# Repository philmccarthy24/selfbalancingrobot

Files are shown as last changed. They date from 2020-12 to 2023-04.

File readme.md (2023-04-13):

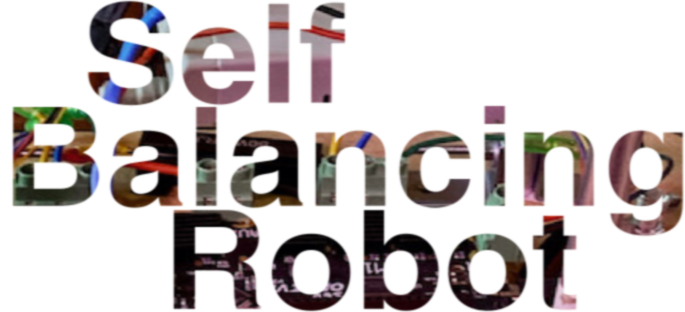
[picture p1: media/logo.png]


## Introduction

A project to explore how self balancing vehicles like the Segway / hoverboards work. This will be a long running spare-time project.

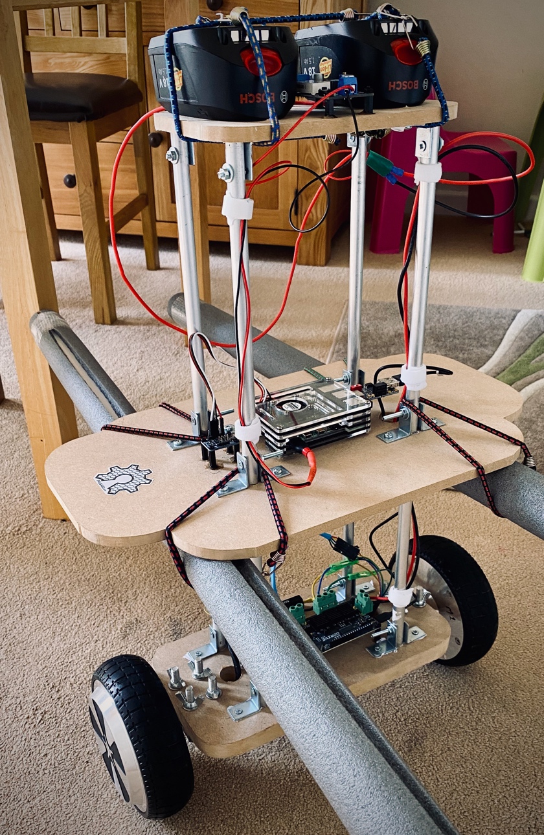
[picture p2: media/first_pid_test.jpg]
first test


## Hardware spec

The robot has been built using:

- 3 layers of MDF, the bottom 18mm thick and the top two 9mm thick
- 4 12mm diameter hollow aluminium poles 50mm in length slotted and bolted through the middle sheet to give strength and stability while keeping the assembly relatively lightweight - fully built, the robot has XX g mass.
- 28 25mm steel braces and 16 M4 bolts/washers/nuts to secure the poles to the boards.
- 2 6.5 inch 36v rated wheel hub motors taken from a broken hoverhoard bought off ebay for £20, each secured with 4 M8 bolts, washers and wing nuts.

See the mechanical drawings in the docs/mechanical directory for further details (created with [OpenSCAD](https://openscad.org/)). Here's a photo of the assembly during motor/ahrs testing, showing how the frame is bolted together:

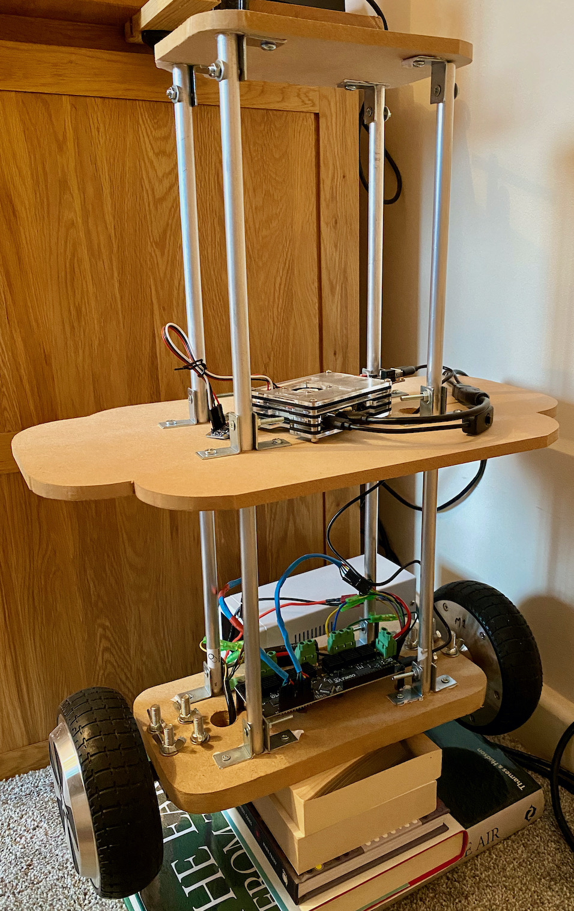
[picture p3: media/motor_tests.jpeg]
motor tests


## Electronics

The motor driver runs on 36v from two 18v LIon batteries I had knocking about from a dead electric screwdriver. 

The controller runs off a separate 18650 LIon battery (to prevent ground loops via ODrive UART connection) via a 3.7v to 5v up-converter.

A Teensy 4.1 MCU runs the control firmware, and is connected to:

- a FXAS2100 Gyroscope IC over I2C bus
- a FXOS8700 Accelerometer/Magnetometer IC over I2C bus
- a 128x64 OLED display over I2C bus
- 3 rotary encoders for user interaction
- a 18-56v [ODrive 3.6 BLDC motor controller board](https://odriverobotics.com) over a serial link at 115200 baud

The sensor hardware containing the gyro/accelerometer/mag sensors is an [Adafruit NXP 9-DOF Breakout Board](https://www.adafruit.com/product/3463).

The wheel hub motors are driven by the ODrive at 36v.

## Firmware

Coded using Arduino IDE, the firmware separates concerns using a basic (synchronous) EventBus PUB/SUB design, to decouple the different elements and allow classes to house library setup boilerplate. 

In this way, the main .ino sketch is kept minimal. `UserInterface` contains a state machine that describes which mode the controller is in. `RotaryEncoder` objects raise position update or button pushed events which are received by the `UserInterface` object, and depending on state either change between screens or allow PID contants to be tweaked (possibly more settings can be managed in future). The main loop periodically fires a timer message at 100Hz, which is received by the `AHRS` object. The handler then reads gyro/accelerometer/magnetometer raw counts from the NXP sensor module, applies NXP/Kalman sensor fusion, and then publishes an AHRS update message on the bus.
`UserInterface` reads AHRS messages and displays data to the screen every 200ms (to avoid timings going out of sync).

`MotionController` also receives AHRS update messages, and uses the values in a PID controller to command the ODrive via serial link to apply current to the wheel motors to keep the robot upright (by moving the robot to keep the weight over the wheels).

## Project restart April 2023

Initially the project used a Raspberry Pi 4 to control the ODrive. I could not get the robot to balance, experiencing violent wheel oscillation motion and instability despite experimenting with lots of PID values. Eventually the ODrive stopped driving one of the motors after a firmware update and failed recalibration.

Several things were wrong with this approach:

- Using a full Linux computer to perform real time motion control; a dedicated MCU is a better choice and allows timings to be more accurate, free of thread scheduling and OS jitter
- Applying velocity commands to ODrive. Current control is better, proportional to torque and more likely to result in successful balance control
- Not having an immediate way to dynamically tweak PID values, resulting in long experimentation cycles. Rotary Encoders and a little OLED screen will save tons of time.

In early April 2023 I dusted off (literally) the robot, flashed the ODrive with the latest firmware, and tried recalibrating the hub motors from scratch. This time I was successful, probably due to updated firmware and instructions. I managed to create a simple sketch for a Teensy 4.1 to drive the wheels via the ODrive serial pins.

I'm now creating a minimal firmware to periodically take AHRS readings, and apply current to the ODrive via a PID controller.

---

## Progress as of May 2021

- Mechanical frame built.
- 36v (2 x 18v) batteries lashed to top panel with bungee cords, and connected via spade terminals to power bus.
- On/off power rocker switch installed.
- 36v to 5v DC down converter connected to power bus and wired to USB-C cable for Pi4 power.
- Odrive board and wheels installed, wiring complete.
- Pi4 with AHRS breakout installed, wiring complete.
- Basic motor calibration done, tested moving hub motors using serial commands issued from Pi4 daemon. *Optimisation with odrivetool required*
- Attached impact lances to frame, to cushion robot during the rather violent oscillations of PID tuning
- Daemon software 95% implemented
  - CMake build system
  - Factories
  - Logging via spdlog library
  - Unit tests via google test library
  - Performance unit tests written to test AHRS at rest and drive motors via ODrive
  - AHRS system to determine orientation in 3D space
  - Gyroscope, accelerometer and magnetometer sensor calibration tool finished, and used to calibrate sensors in-situ after installation on chassis
  - Motor controller api
  - PID controller
- UI software barely started
  - Non-TS React interface started
  - Tested against a fake REST controller served by Node.js
  
#### TO DO:

- Write gRPC service in daemon to support remote drive control
- Complete React UI
- Complete tuning PID controller to make the robot stay up. 

## License/legal

Copyright (c) 2021 Phil McCarthy

Provided under the [MIT License](https://github.com/philmccarthy24/selfbalancingrobot/blob/8f1a7e7f0787cc03bbfced4b563601a9d68a3980/LICENSE).

The software uses the following open source libraries, with thanks and appreciation to their maintainers:

- [Bosch Power4All adapter design](https://github.com/usedbytes/power4all) base part Copyright 2020 Brian Starkey
- Adafruit SSD1306 and dependencies (OLED)
- Encoder (rotary encoders)
- Afafruit_AHRS (with FXOS/FXAS deps)
- [ODrive Arduino](https://github.com/odriverobotics/ODrive/tree/master/Arduino/ODriveArduino)

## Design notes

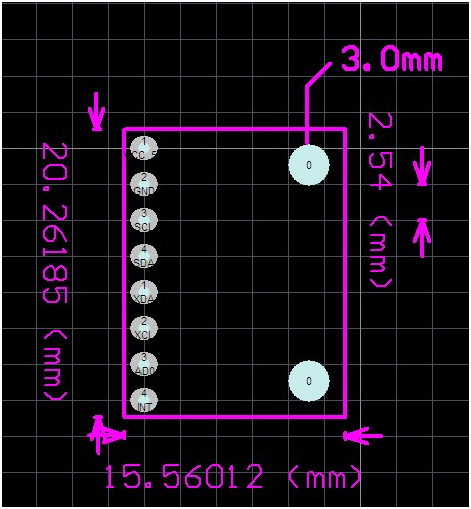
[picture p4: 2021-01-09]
docs/mechanical/MPU6050-Dimensions.png

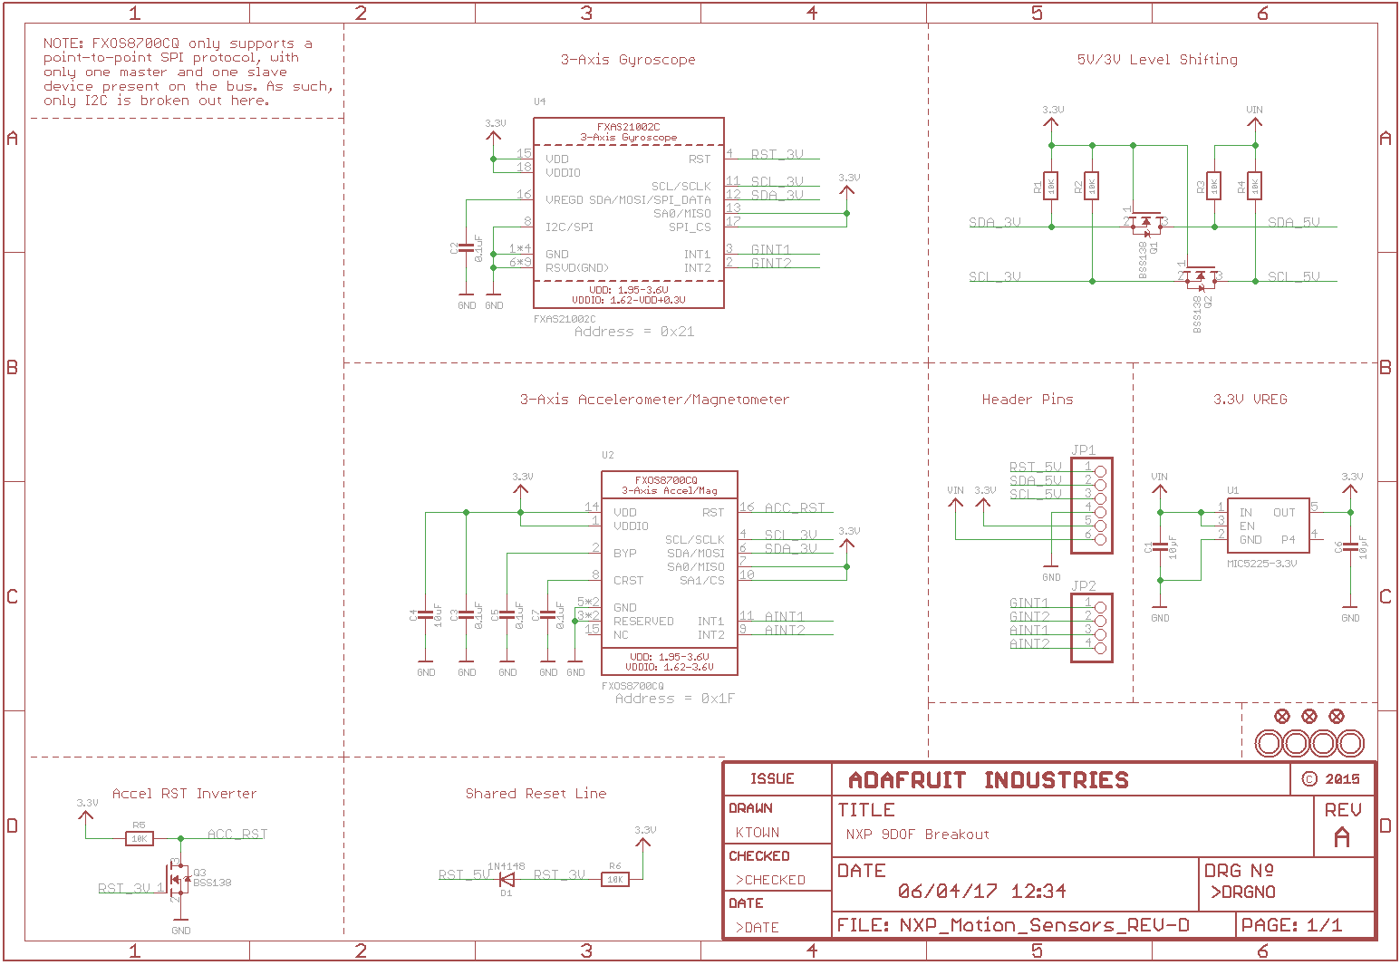
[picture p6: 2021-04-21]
docs/sensors_NXPPrecision9DOF.png

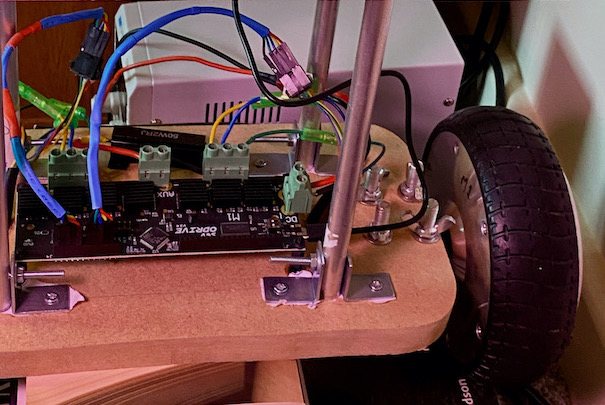
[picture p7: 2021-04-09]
media/controller.jpeg

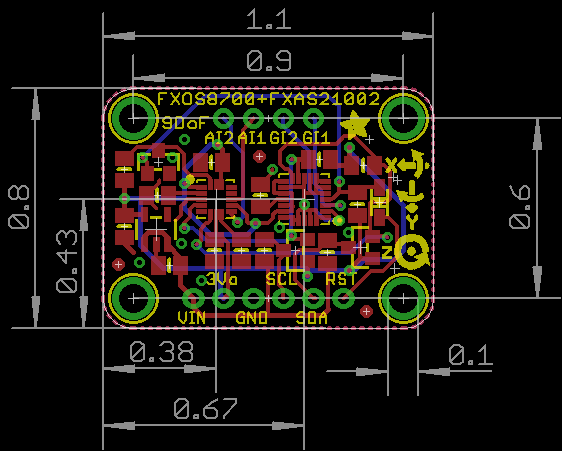
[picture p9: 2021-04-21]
docs/nxp_precision_9dof_breakout.png

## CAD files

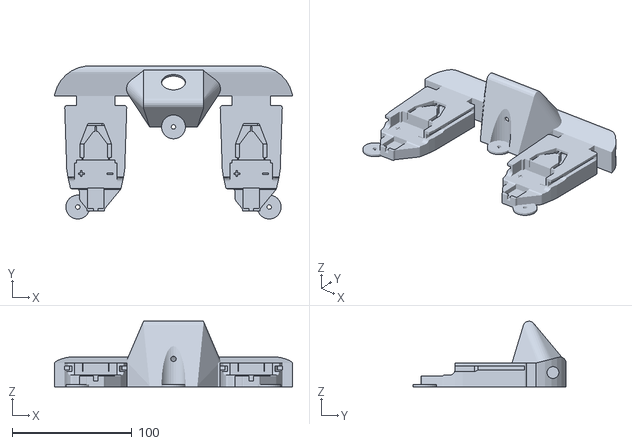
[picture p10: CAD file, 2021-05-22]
cad/batterymount/power4allmount.stl
198.9 x 127.8 x 55.0

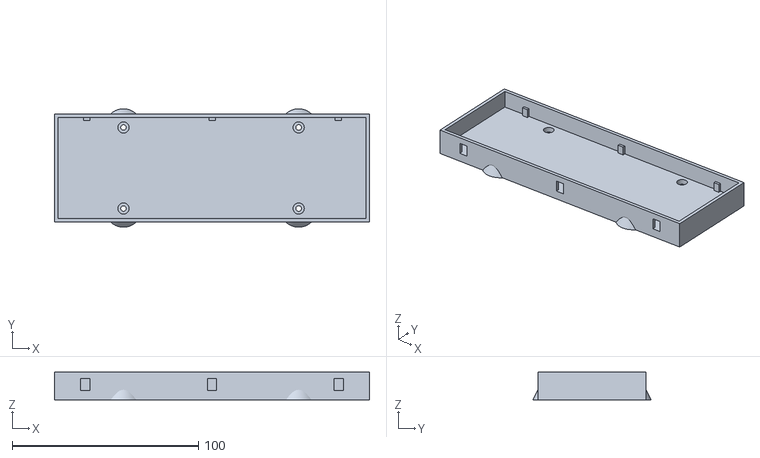
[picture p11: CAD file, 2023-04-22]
cad/stl/prototype_breadboard_mount.stl
169.0 x 63.5 x 15.0

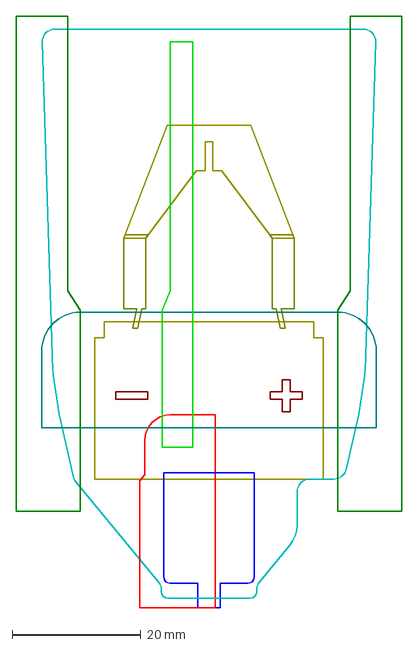
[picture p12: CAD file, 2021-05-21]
cad/batterymount/power4all.dxf
60.0 x 92.0 mm

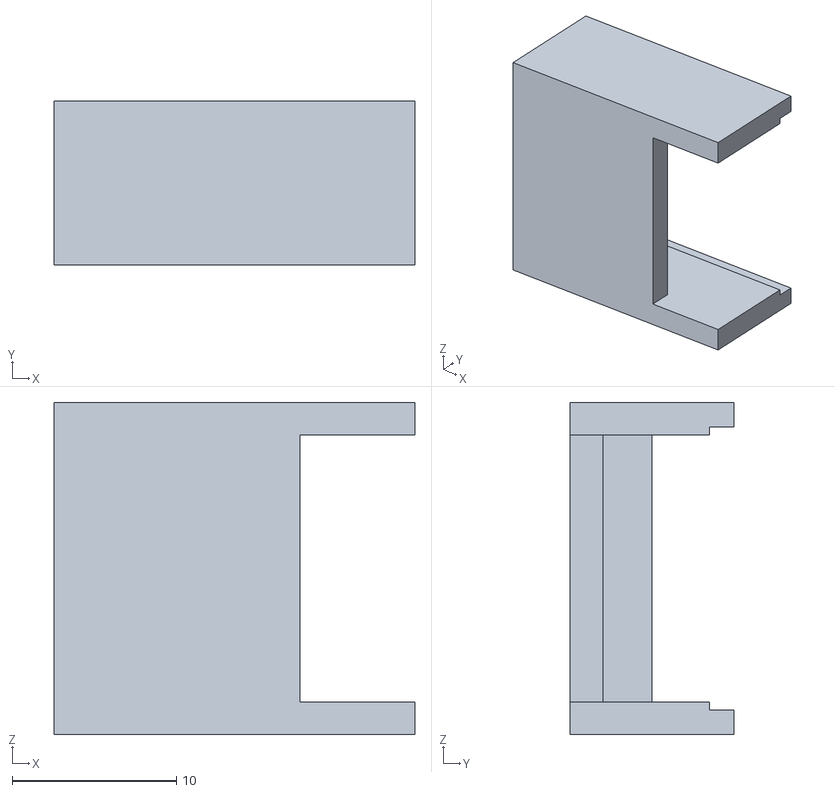
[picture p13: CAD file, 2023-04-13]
cad/stl/tp4056mount.stl
22.0 x 10.0 x 20.2

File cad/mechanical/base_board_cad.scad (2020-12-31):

// globals
board_width = 295;
board_height = 150;

include <common.scad>

difference() {
    union() {
        rounded_rectangle(board_width, board_height, 30);
    }
    
    union() {
        stator_axle_plate_width = 40;
        stator_axle_plate_height = 44;
        axle_plate_bolt_holes = [[7.5, 6.5], [32, 6.5], [7.5, 36.5], [32, 36.5]];
        // left plate bolt holes
        // to secure stator axle, will need M8 bolts at least 55mm shaft length (not including head. head diameter must be no more than 12mm)
        circle_group( axle_plate_bolt_holes, 8, [0, (board_height/2) - (stator_axle_plate_height/2)]);
        
        // left cable hole
        offset_circle([stator_axle_plate_width + 20, board_height/2], 20);
       
        // odrive mounting holes
        odrive_width = 140.5;
        odrive_height = 50;
        odrive_left_edge = stator_axle_plate_width + 20 + 20;
        odrive_standoff_mounting_holes = [[2.5,4], [2.5,47.5], [55,5.5], [55,29.1], [93.5,5.5], [93.5,29.1], [138,4], [138,47.5]];
        circle_group( odrive_standoff_mounting_holes, 6, [odrive_left_edge, (board_height/2) - (odrive_height/2) + 15]);
        
        // support rods and mounting bracket holes
        top_board_pt_offset = [(board_width/2) - (top_board_width/2),board_height-top_board_height-5];
        support_rods_and_bracket_holes(true, top_board_pt_offset);
        
        // right cable hole
        offset_circle([odrive_left_edge + odrive_width + 15, board_height/2], 20);
        
        // right plate bolt holes
        circle_group( axle_plate_bolt_holes, 8, [board_width-stator_axle_plate_width, (board_height/2) - (stator_axle_plate_height/2)]);
    }
}

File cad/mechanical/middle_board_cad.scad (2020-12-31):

// globals
board_width_extent = 295+140;
board_height_extent = 250;

include <common.scad>

top_board_pt_offset = [(board_width_extent/2) - (top_board_width/2),(board_height_extent/2)-(top_board_height/2)];

difference() {
    union() {
        translate([0,20])
            rounded_rectangle(board_width_extent, board_height_extent*0.7, 50);
        
        middle_section_width = board_width_extent*0.75;
        translate([(board_width_extent/2)-(middle_section_width/2),0])
            rounded_rectangle(middle_section_width, board_height_extent, 50);
    }
    
    union() {
        support_rods_and_bracket_holes(true, top_board_pt_offset);
        
        // cable and data hole
        translate([20,top_board_height-50])
            offset_circle(top_board_pt_offset, 20);
    }
}

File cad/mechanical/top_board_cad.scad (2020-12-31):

include <common.scad>

difference() {
    union() {
        rounded_rectangle(top_board_width, top_board_height, 30);
    }
    
    union() {
        support_rods_and_bracket_holes(false);
    }
}

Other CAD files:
cad/batterymount/power4all.scad
cad/batterymount/power4allmount.scad
cad/mcuenclosure/powermodule.scad
cad/mcuenclosure/prototype_powerbank_mount.scad
cad/mechanical/common.scad

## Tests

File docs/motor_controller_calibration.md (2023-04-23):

# Reproduction steps for motor controller calibration

## Hardware

- ODrive 3.6 56v version https://odriverobotics.com
- 2 x 6.5" 36V Hoverboard wheels (Lanba36V20B191025724/800 - SN?)
- 36V power supply
- Raspberry PI 4 running off seperate power supply to avoid ground loops

### Wiring setup

Follow [the ODrive setup guide](https://docs.odriverobotics.com/) for the hardware connection guide (diagram below)

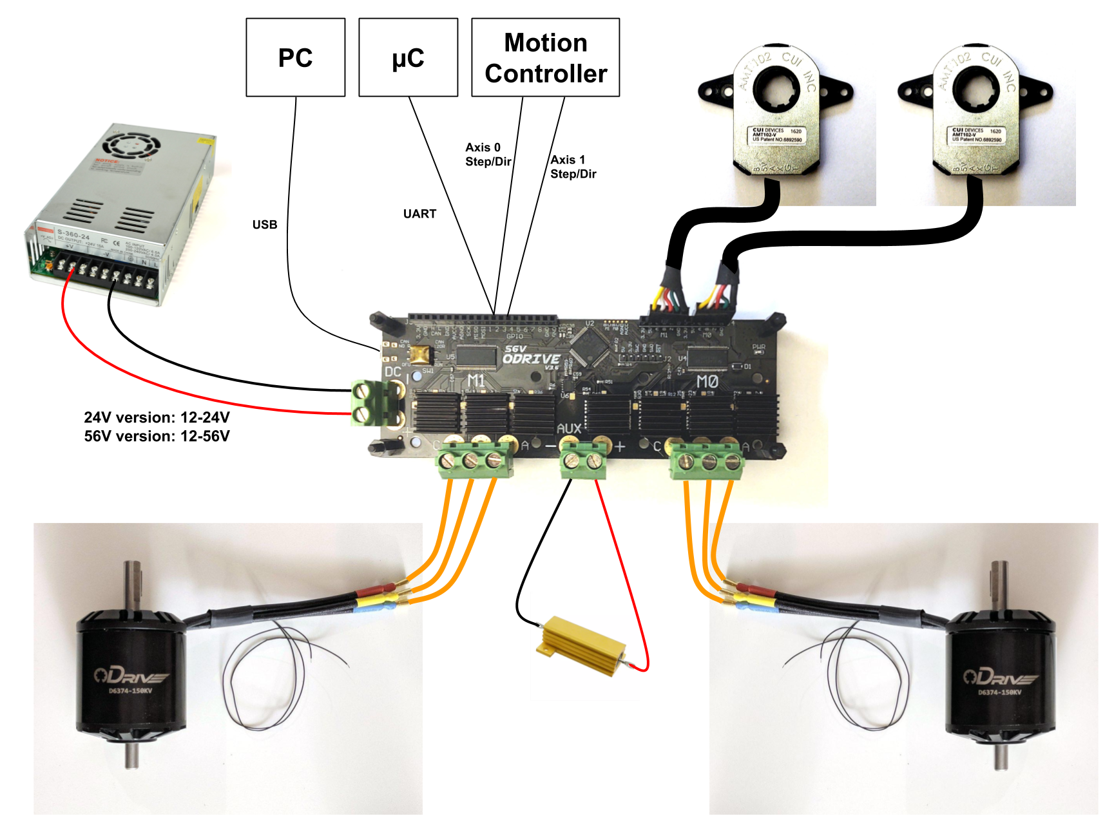
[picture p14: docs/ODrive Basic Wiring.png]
Wiring guide


#### Hall sensor wiring

- Red : 5V
- Yellow : A
- Blue : B
- Green : Z
- Black : GND

# Software

On Raspberry PI

```
sudo pip3 install --upgrade odrive
sudo odrivetool
```

Should now be in interactive ODrive tool ready to issue setup / calibration commands.

Hoverboard specific guide is [here](https://docs.odriverobotics.com/v/0.5.5/hoverboard.html#hoverboard-doc), info extracted and summarised for posterity. This is what worked for me and the second hand hoverboard motors after some tweaking and errors about motor phase inductance.
Set axis0 or axis1 depending on if M0 or M1 is being setup.

```
odrv0.axis0.motor.config.pole_pairs = 15

odrv0.axis0.motor.config.resistance_calib_max_voltage = 4
odrv0.axis0.motor.config.calibration_current = 5 # this was added to get calib to work - NOT IN GUIDE. default was 10
odrv0.axis0.motor.config.requested_current_range = 25 #Requires config save and reboot
odrv0.axis0.motor.config.current_control_bandwidth = 100
odrv0.axis0.motor.config.torque_constant = 8.27 / 16

odrv0.axis0.encoder.config.mode = ENCODER_MODE_HALL
odrv0.axis0.encoder.config.cpr = 90
odrv0.axis0.encoder.config.calib_scan_distance = 150
odrv0.config.gpio9_mode = GPIO_MODE_DIGITAL
odrv0.config.gpio10_mode = GPIO_MODE_DIGITAL
odrv0.config.gpio11_mode = GPIO_MODE_DIGITAL

odrv0.axis0.encoder.config.bandwidth = 100
odrv0.axis0.controller.config.pos_gain = 1
odrv0.axis0.controller.config.vel_gain = 0.02 * odrv0.axis0.motor.config.torque_constant * odrv0.axis0.encoder.config.cpr
odrv0.axis0.controller.config.vel_integrator_gain = 0.1 * odrv0.axis0.motor.config.torque_constant * odrv0.axis0.encoder.config.cpr
odrv0.axis0.controller.config.vel_limit = 10
odrv0.axis0.controller.config.control_mode = CONTROL_MODE_VELOCITY_CONTROL

odrv0.save_configuration()
odrv0.reboot()

# do the calibration
odrv0.axis0.requested_state = AXIS_STATE_MOTOR_CALIBRATION

# read out data pertaining to motor
odrv0.axis0.motor

# error should be 0x0000 and phase_inductance / phase_resistance should be set (not 0.0)
# tell the ODrive that saving this calibration to persistent memory is OK
odrv0.axis0.motor.config.pre_calibrated = True

odrv0.axis0.requested_state = AXIS_STATE_ENCODER_HALL_POLARITY_CALIBRATION

# read out status of encoder
odrv0.axis0.encoder

# error should be 0x0000

# check the alignment between the motor and the hall sensor
odrv0.axis0.requested_state = AXIS_STATE_ENCODER_OFFSET_CALIBRATION

# read out status of encoder
odrv0.axis0.encoder

# error should be 0x0000 and phase_offset_float should be -1.5, -0.5, 0.5 or 1.5
# tell the ODrive that saving this calibration to persistent memory is OK
odrv0.axis0.encoder.config.pre_calibrated = True

# Save, reboot, and test! ODrive starts in IDLE by default (can configure this), so need to enable closed loop control.
odrv0.save_configuration()
odrv0.reboot()

odrv0.axis0.requested_state = AXIS_STATE_CLOSED_LOOP_CONTROL
odrv0.axis0.controller.input_vel = 2
# Your motor should spin here!!!!
odrv0.axis0.controller.input_vel = 0
odrv0.axis0.requested_state = AXIS_STATE_IDLE
```

Repeat for axis1 (text here for easy copy-paste):

```
odrv0.axis1.motor.config.pole_pairs = 15

odrv0.axis1.motor.config.resistance_calib_max_voltage = 4
odrv0.axis1.motor.config.calibration_current = 5 # this was added to get calib to work - NOT IN GUIDE. default was 10
odrv0.axis1.motor.config.requested_current_range = 25 #Requires config save and reboot
odrv0.axis1.motor.config.current_control_bandwidth = 100
odrv0.axis1.motor.config.torque_constant = 8.27 / 16

odrv0.axis1.encoder.config.mode = ENCODER_MODE_HALL
odrv0.axis1.encoder.config.cpr = 90
odrv0.axis1.encoder.config.calib_scan_distance = 150
odrv0.config.gpio9_mode = GPIO_MODE_DIGITAL
odrv0.config.gpio10_mode = GPIO_MODE_DIGITAL
odrv0.config.gpio11_mode = GPIO_MODE_DIGITAL

odrv0.axis1.encoder.config.bandwidth = 100
odrv0.axis1.controller.config.pos_gain = 1
odrv0.axis1.controller.config.vel_gain = 0.02 * odrv0.axis0.motor.config.torque_constant * odrv0.axis0.encoder.config.cpr
odrv0.axis1.controller.config.vel_integrator_gain = 0.1 * odrv0.axis0.motor.config.torque_constant * odrv0.axis0.encoder.config.cpr
odrv0.axis1.controller.config.vel_limit = 10
odrv0.axis1.controller.config.control_mode = CONTROL_MODE_VELOCITY_CONTROL

odrv0.save_configuration()
odrv0.reboot()

# do the calibration
odrv0.axis1.requested_state = AXIS_STATE_MOTOR_CALIBRATION

# read out data pertaining to motor
odrv0.axis1.motor

# error should be 0x0000 and phase_inductance / phase_resistance should be set (not 0.0)
# tell the ODrive that saving this calibration to persistent memory is OK
odrv0.axis1.motor.config.pre_calibrated = True

odrv0.axis1.requested_state = AXIS_STATE_ENCODER_HALL_POLARITY_CALIBRATION

# read out status of encoder
odrv0.axis1.encoder

# error should be 0x0000

# check the alignment between the motor and the hall sensor
odrv0.axis1.requested_state = AXIS_STATE_ENCODER_OFFSET_CALIBRATION

# read out status of encoder
odrv0.axis1.encoder

# error should be 0x0000 and phase_offset_float should be -1.5, -0.5, 0.5 or 1.5
# tell the ODrive that saving this calibration to persistent memory is OK
odrv0.axis1.encoder.config.pre_calibrated = True

# Save, reboot, and test! ODrive starts in IDLE by default (can configure this), so need to enable closed loop control.
odrv0.save_configuration()
odrv0.reboot()

odrv0.axis1.requested_state = AXIS_STATE_CLOSED_LOOP_CONTROL
odrv0.axis1.controller.input_vel = 2
# Your motor should spin here!!!!
odrv0.axis1.controller.input_vel = 0
odrv0.axis1.requested_state = AXIS_STATE_IDLE
```

We then need to put the odrive in TORQUE_CONTROL mode with 

```
odrv0.axis0.controller.config.control_mode = ControlMode.TORQUE_CONTROL
odrv0.axis1.controller.config.control_mode = ControlMode.TORQUE_CONTROL
odrv0.axis0.controller.config.enable_torque_mode_vel_limit = False
odrv0.axis1.controller.config.enable_torque_mode_vel_limit = False

```

May also need to disable current limits

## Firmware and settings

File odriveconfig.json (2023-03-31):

{"axis0": {"acim_estimator": {"config": {"slip_velocity": 14.706000328063965}}, "config": {"dir_gpio_pin": 2, "enable_sensorless_mode": false, "enable_step_dir": false, "enable_watchdog": false, "startup_closed_loop_control": false, "startup_encoder_index_search": false, "startup_encoder_offset_calibration": false, "startup_homing": false, "startup_motor_calibration": false, "step_dir_always_on": false, "step_gpio_pin": 1, "watchdog_timeout": 0.0, "calibration_lockin": {"accel": 20.0, "current": 10.0, "ramp_distance": 3.1415927410125732, "ramp_time": 0.4000000059604645, "vel": 40.0}, "can": {"encoder_rate_ms": 10, "heartbeat_rate_ms": 100, "is_extended": false, "node_id": 0}, "general_lockin": {"accel": 20.0, "current": 10.0, "finish_distance": 100.0, "finish_on_distance": false, "finish_on_enc_idx": false, "finish_on_vel": false, "ramp_distance": 3.1415927410125732, "ramp_time": 0.4000000059604645, "vel": 40.0}, "sensorless_ramp": {"accel": 200.0, "current": 10.0, "finish_distance": 100.0, "finish_on_distance": false, "finish_on_enc_idx": false, "finish_on_vel": true, "ramp_distance": 3.1415927410125732, "ramp_time": 0.4000000059604645, "vel": 400.0}}, "controller": {"config": {"axis_to_mirror": 255, "circular_setpoint_range": 1.0, "circular_setpoints": false, "control_mode": 2, "electrical_power_bandwidth": 20.0, "enable_gain_scheduling": false, "enable_overspeed_error": true, "enable_torque_mode_vel_limit": true, "enable_vel_limit": true, "gain_scheduling_width": 10.0, "homing_speed": 0.25, "inertia": 0.0, "input_filter_bandwidth": 2.0, "input_mode": 1, "load_encoder_axis": 0, "mechanical_power_bandwidth": 20.0, "mirror_ratio": 1.0, "pos_gain": 1.0, "spinout_electrical_power_threshold": 10.0, "spinout_mechanical_power_threshold": -10.0, "steps_per_circular_range": 1024, "torque_mirror_ratio": 0.0, "torque_ramp_rate": 0.009999999776482582, "vel_gain": 0.9303750395774841, "vel_integrator_gain": 4.6518754959106445, "vel_integrator_limit": Infinity, "vel_limit": 10.0, "vel_limit_tolerance": 1.2000000476837158, "vel_ramp_rate": 1.0, "anticogging": {"anticogging_enabled": true, "calib_anticogging": false, "calib_pos_threshold": 1.0, "calib_vel_threshold": 1.0, "cogging_ratio": 1.0, "index": 0, "pre_calibrated": false}}}, "encoder": {"config": {"abs_spi_cs_gpio_pin": 1, "bandwidth": 100.0, "calib_range": 0.019999999552965164, "calib_scan_distance": 150.0, "calib_scan_omega": 12.566370964050293, "cpr": 90, "direction": 1, "enable_phase_interpolation": true, "find_idx_on_lockin_only": false, "hall_polarity_calibrated": true, "hall_polarity": 0, "ignore_illegal_hall_state": false, "index_offset": 0.0, "mode": 1, "phase_offset_float": 1.4461486339569092, "phase_offset": 69, "pre_calibrated": true, "sincos_gpio_pin_cos": 4, "sincos_gpio_pin_sin": 3, "use_index_offset": true, "use_index": false}}, "max_endstop": {"config": {"debounce_ms": 50, "enabled": false, "gpio_num": 0, "is_active_high": false, "offset": 0.0}}, "mechanical_brake": {"config": {"gpio_num": 0, "is_active_low": true}}, "min_endstop": {"config": {"debounce_ms": 50, "enabled": false, "gpio_num": 0, "is_active_high": false, "offset": 0.0}}, "motor": {"config": {"I_bus_hard_max": Infinity, "I_bus_hard_min": -Infinity, "I_leak_max": 0.10000000149011612, "R_wL_FF_enable": false, "acim_autoflux_attack_gain": 10.0, "acim_autoflux_decay_gain": 1.0, "acim_autoflux_enable": false, "acim_autoflux_min_Id": 10.0, "acim_gain_min_flux": 10.0, "bEMF_FF_enable": false, "calibration_current": 5.0, "current_control_bandwidth": 100.0, "current_lim_margin": 8.0, "current_lim": 10.0, "dc_calib_tau": 0.20000000298023224, "inverter_temp_limit_lower": 100.0, "inverter_temp_limit_upper": 120.0, "motor_type": 0, "phase_inductance": 0.0006406255415640771, "phase_resistance": 0.553097128868103, "pole_pairs": 15, "pre_calibrated": true, "requested_current_range": 25.0, "resistance_calib_max_voltage": 4.0, "torque_constant": 0.5168750286102295, "torque_lim": Infinity}, "fet_thermistor": {"config": {"enabled": true, "temp_limit_lower": 100.0, "temp_limit_upper": 120.0}}, "motor_thermistor": {"config": {"enabled": false, "gpio_pin": 4, "poly_coefficient_0": 0.0, "poly_coefficient_1": 0.0, "poly_coefficient_2": 0.0, "poly_coefficient_3": 0.0, "temp_limit_lower": 100.0, "temp_limit_upper": 120.0}}}, "sensorless_estimator": {"config": {"observer_gain": 1000.0, "pll_bandwidth": 1000.0, "pm_flux_linkage": 0.0015800000401213765}}, "trap_traj": {"config": {"accel_limit": 0.5, "decel_limit": 0.5, "vel_limit": 2.0}}}, "axis1": {"acim_estimator": {"config": {"slip_velocity": 14.706000328063965}}, "config": {"dir_gpio_pin": 8, "enable_sensorless_mode": false, "enable_step_dir": false, "enable_watchdog": false, "startup_closed_loop_control": false, "startup_encoder_index_search": false, "startup_encoder_offset_calibration": false, "startup_homing": false, "startup_motor_calibration": false, "step_dir_always_on": false, "step_gpio_pin": 7, "watchdog_timeout": 0.0, "calibration_lockin": {"accel": 20.0, "current": 10.0, "ramp_distance": 3.1415927410125732, "ramp_time": 0.4000000059604645, "vel": 40.0}, "can": {"encoder_rate_ms": 10, "heartbeat_rate_ms": 100, "is_extended": false, "node_id": 1}, "general_lockin": {"accel": 20.0, "current": 10.0, "finish_distance": 100.0, "finish_on_distance": false, "finish_on_enc_idx": false, "finish_on_vel": false, "ramp_distance": 3.1415927410125732, "ramp_time": 0.4000000059604645, "vel": 40.0}, "sensorless_ramp": {"accel": 200.0, "current": 10.0, "finish_distance": 100.0, "finish_on_distance": false, "finish_on_enc_idx": false, "finish_on_vel": true, "ramp_distance": 3.1415927410125732, "ramp_time": 0.4000000059604645, "vel": 400.0}}, "controller": {"config": {"axis_to_mirror": 255, "circular_setpoint_range": 1.0, "circular_setpoints": false, "control_mode": 2, "electrical_power_bandwidth": 20.0, "enable_gain_scheduling": false, "enable_overspeed_error": true, "enable_torque_mode_vel_limit": true, "enable_vel_limit": true, "gain_scheduling_width": 10.0, "homing_speed": 0.25, "inertia": 0.0, "input_filter_bandwidth": 2.0, "input_mode": 1, "load_encoder_axis": 1, "mechanical_power_bandwidth": 20.0, "mirror_ratio": 1.0, "pos_gain": 1.0, "spinout_electrical_power_threshold": 10.0, "spinout_mechanical_power_threshold": -10.0, "steps_per_circular_range": 1024, "torque_mirror_ratio": 0.0, "torque_ramp_rate": 0.009999999776482582, "vel_gain": 0.9303750395774841, "vel_integrator_gain": 4.6518754959106445, "vel_integrator_limit": Infinity, "vel_limit": 10.0, "vel_limit_tolerance": 1.2000000476837158, "vel_ramp_rate": 1.0, "anticogging": {"anticogging_enabled": true, "calib_anticogging": false, "calib_pos_threshold": 1.0, "calib_vel_threshold": 1.0, "cogging_ratio": 1.0, "index": 0, "pre_calibrated": false}}}, "encoder": {"config": {"abs_spi_cs_gpio_pin": 1, "bandwidth": 100.0, "calib_range": 0.019999999552965164, "calib_scan_distance": 150.0, "calib_scan_omega": 12.566370964050293, "cpr": 90, "direction": 1, "enable_phase_interpolation": true, "find_idx_on_lockin_only": false, "hall_polarity_calibrated": true, "hall_polarity": 0, "ignore_illegal_hall_state": false, "index_offset": 0.0, "mode": 1, "phase_offset_float": 1.4460649490356445, "phase_offset": 69, "pre_calibrated": true, "sincos_gpio_pin_cos": 4, "sincos_gpio_pin_sin": 3, "use_index_offset": true, "use_index": false}}, "max_endstop": {"config": {"debounce_ms": 50, "enabled": false, "gpio_num": 0, "is_active_high": false, "offset": 0.0}}, "mechanical_brake": {"config": {"gpio_num": 0, "is_active_low": true}}, "min_endstop": {"config": {"debounce_ms": 50, "enabled": false, "gpio_num": 0, "is_active_high": false, "offset": 0.0}}, "motor": {"config": {"I_bus_hard_max": Infinity, "I_bus_hard_min": -Infinity, "I_leak_max": 0.10000000149011612, "R_wL_FF_enable": false, "acim_autoflux_attack_gain": 10.0, "acim_autoflux_decay_gain": 1.0, "acim_autoflux_enable": false, "acim_autoflux_min_Id": 10.0, "acim_gain_min_flux": 10.0, "bEMF_FF_enable": false, "calibration_current": 5.0, "current_control_bandwidth": 100.0, "current_lim_margin": 8.0, "current_lim": 10.0, "dc_calib_tau": 0.20000000298023224, "inverter_temp_limit_lower": 100.0, "inverter_temp_limit_upper": 120.0, "motor_type": 0, "phase_inductance": 0.0006110583199188113, "phase_resistance": 0.5124536752700806, "pole_pairs": 15, "pre_calibrated": true, "requested_current_range": 25.0, "resistance_calib_max_voltage": 4.0, "torque_constant": 0.5168750286102295, "torque_lim": Infinity}, "fet_thermistor": {"config": {"enabled": true, "temp_limit_lower": 100.0, "temp_limit_upper": 120.0}}, "motor_thermistor": {"config": {"enabled": false, "gpio_pin": 4, "poly_coefficient_0": 0.0, "poly_coefficient_1": 0.0, "poly_coefficient_2": 0.0, "poly_coefficient_3": 0.0, "temp_limit_lower": 100.0, "temp_limit_upper": 120.0}}}, "sensorless_estimator": {"config": {"observer_gain": 1000.0, "pll_bandwidth": 1000.0, "pm_flux_linkage": 0.0015800000401213765}}, "trap_traj": {"config": {"accel_limit": 0.5,
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

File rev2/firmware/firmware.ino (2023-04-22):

#include <Wire.h>
#include <elapsedMillis.h>
#include "EventBus.h"
#include "RotaryEncoder.h"
#include "UserInterface.h"
#include "AHRS.h"
#include "MotionController.h"
#include <ArduinoLog.h>

EventBus eventBus;
UserInterface gui(&eventBus);
RotaryEncoder dial1(0, 34, 35, 26, &eventBus);
RotaryEncoder dial2(1, 38, 37, 27, &eventBus);
//RotaryEncoder dial3(2, 40, 39, 28, &eventBus);
AHRS ahrs(&eventBus);
MotionController motionController(&eventBus);

elapsedMillis msTimer;
const int AHRS_PERIOD_MS = 1000 / FILTER_UPDATE_RATE_HZ;

void setup() {
  Serial.begin(115200);
  while (!Serial) {} // wait for serial interace to connect

  Log.begin(LOG_LEVEL_VERBOSE, &Serial);

  Log.traceln(F("Setting I2C clock to 400kHz"));
  Wire.setClock(400000); // set I2C clock to 400KHz - ahrs seems to need this

  Log.traceln(F("Setting up event subscriptions..."));
  // setup message subscriptions
  eventBus.Subscribe(&ahrs);
  eventBus.Subscribe(&gui);
  eventBus.Subscribe(&motionController);

  if (!gui.Initialise() || !ahrs.Initialise() || !motionController.Initialise())
    for(;;) // Printed errors to serial already - so spin forever

  Log.traceln(F("Initialised"));
}

void loop() {
  // poll physical controls - this could result in events being fired
  dial1.Poll();
  dial2.Poll();
  //dial3.Poll();

  // publish a timer message every 10ms, to trigger
  // AHRS and then consequentially motion control
  if (msTimer >= AHRS_PERIOD_MS) {
    msTimer = msTimer - AHRS_PERIOD_MS;
    eventBus.Publish(0, EEventType::TimerTimeout, &AHRS_PERIOD_MS);
  }
}

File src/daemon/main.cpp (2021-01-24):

#include <iostream>
#include <memory>
#include <unistd.h>
#include "Register.h"
#include "SBRProdFactory.h"

using namespace std;
using namespace sbrcontroller;

int main()
{
    try {
        // production startup process
        utility::Register::RegisterFactory(make_shared<utility::SBRProdFactory>("./sbrconfig.json"));
        auto ahrsDataSource = utility::Register::Factory.CreateAHRSDataSource();

        for (int i = 0; i < 100; i++) {
            auto currOrientation = ahrsDataSource->ReadOrientation();
            cout << "X rotation " << currOrientation. << " degrees, Y rotation " << currOrientation.m_dbPitch_deg << "degrees" << endl;
            usleep(100 * 1000);
            // seem to be drifting quite a bit (+/- 1degree) even when still. is this
            // sensor noise?
            // https://wired.chillibasket.com/2015/01/calibrating-mpu6050/ has some stuff about
            // fifo. calibrate? read from mp fifo?
            // raw signal synchronisation issue?? https://electronics.stackexchange.com/questions/333174/mpu6050-accel-gyro-noise-that-behaves-strangely-what-might-be-doing-this
        }
    }
    catch (const std::exception& ex) {
        cout << ex.what() << endl;
    }
}

//https://code.visualstudio.com/docs/languages/cpp

//http://wiringpi.com/reference/i2c-library/

//https://sudonull.com/post/97828-Ruby-and-C-Part-4-Friends-of-the-accelerometer-gyroscope-and-range-finder-with-Raphaeljs


//https://wiki.dfrobot.com/How_to_Use_a_Three-Axis_Accelerometer_for_Tilt_Sensing ??

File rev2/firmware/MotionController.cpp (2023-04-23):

#include "MotionController.h"
#include "AHRS.h"
#include <EEPROM.h>
#include <HardwareSerial.h>
#include <ODriveArduino.h>
#include <Wire.h>
#include <Arduino.h>
#include <ArduinoLog.h>

#define MOTION_CONTROLLER_SETTINGS_EEPROM_ADDRESS 140

// Printing with stream operator helper functions
template<class T> inline Print& operator <<(Print &obj,     T arg) { obj.print(arg);    return obj; }
template<>        inline Print& operator <<(Print &obj, float arg) { obj.print(arg, 4); return obj; }

// Teensy 4.1 - Serial1
// pin 0: RX - connect to ODrive TX (GPIO pin 1 on ODrive)
// pin 1: TX - connect to ODrive RX (GPIO pin 2 on ODrive)
HardwareSerial& odrive_serial = Serial1;
ODriveArduino odrive(odrive_serial);

MotionController::MotionController(EventBus* pEventBus) : 
  m_pEventBus(pEventBus)
{
}

bool MotionController::Initialise()
{
  Log.traceln(F("MotionController::Initialise"));

  //read eeprom at offset 140 to get persisted Kp,Ki,Kd constants
  float Kpid[3];
  EEPROM.get(MOTION_CONTROLLER_SETTINGS_EEPROM_ADDRESS,Kpid);
  if (isnan(Kpid[0]) || isnan(Kpid[1]) || isnan(Kpid[2]))
  {
    Log.traceln(F("PID constants not set, initialising to 0.0..."));
    Kpid[0] = 0.0f;
    Kpid[1] = 0.0f;
    Kpid[2] = 0.0f;
    EEPROM.put(MOTION_CONTROLLER_SETTINGS_EEPROM_ADDRESS,Kpid);
    Log.traceln(F("PID constants initialised."));
  }
  m_Kp = Kpid[0];
  m_Ki = Kpid[1];
  m_Kd = Kpid[2];

  Log.traceln(F("Read PID vals from EEPROM: Kp=%F, Kd=%F"), m_Kp, m_Kd);

  // publish a message with read settings, to synchronise interested listeners
  m_pEventBus->Publish(0, EEventType::SettingsSync, Kpid);

  // ODrive uses 115200 baud
  odrive_serial.begin(115200);

  Log.traceln(F("Setting ODrive current limits to 10A per wheel"));
  //odrive_serial << "w axis0.motor.config.current_lim " << 5.0f << '\n';
  //odrive_serial << "w axis1.motor.config.current_lim " << 5.0f << '\n';

  odrive_serial << "w axis0.controller.config.enable_torque_mode_vel_limit false\n";
  odrive_serial << "w axis1.controller.config.enable_torque_mode_vel_limit false\n";

  int requested_state = AXIS_STATE_CLOSED_LOOP_CONTROL;
  Log.traceln(F("Engaging motors"));
  odrive.run_state(0, requested_state, false);
  odrive.run_state(1, requested_state, false);

  return true;
}

void MotionController::OnEventNotify(int sourceId, EEventType type, const void* eventData)
{
  // AHRS updates tick on a 100hz timer, which we will match to control wheel torque.
  // Note we have the flexibility to change this by creating an additional independent timer, caching AHRS
  // update messages and then doing PID processing and motion control on the independent timer tick.

  if (type == EEventType::AHRSUpdate) {
    SOrientationPayload* pOri = (SOrientationPayload*)eventData;

    // TODO: emergency cutoffs constants as config params rather than hard coded
    float balanceCurrent = 0.0f;
    if (pOri->roll < HALF_PI / 2) // 45 degrees
    {
      balanceCurrent = (m_Kp * pOri->roll) + (m_Kd * pOri->gyroX); //m_Ki integral term redundant for now
    }
    if (balanceCurrent > 10.0f)
      balanceCurrent = 10.0f; // manual current limiter
    
    // log every half second
    if (logTimer >= 500) {
      logTimer = logTimer - 500;
      Log.traceln(F("balanceCurrent set to %F"), balanceCurrent);
    }

    odrive.SetCurrent(0, (float)MOTOR_DIR_M0 * balanceCurrent);
    odrive.SetCurrent(1, (float)MOTOR_DIR_M1 * balanceCurrent);

    // TODO: control via RC
  } else if (type == EEventType::SettingsSync && sourceId == 1) {
    // (cached) PID vals have been updated in UI. Update master ones in this object
    const float* pidArray = (const float*)eventData;
    m_Kp = pidArray[0];
    m_Ki = pidArray[1];
    m_Kd = pidArray[2];
  } else if (type == EEventType::StoreData)
  {
    // persist new pid settings to eeprom
    float Kpid[3];
    Kpid[0] = m_Kp;
    Kpid[1] = m_Ki;
    Kpid[2] = m_Kd;
    EEPROM.put(MOTION_CONTROLLER_SETTINGS_EEPROM_ADDRESS,Kpid);
  }
}

/*
// standby function
void MotionController::Control() 
{
  Serial.println("Setting current on motors");
  
  delay(5000);
  int requested_state = AXIS_STATE_CLOSED_LOOP_CONTROL;
  Serial.println("Engaging motors");
  odrive.run_state(0, requested_state, false);
  odrive.run_state(1, requested_state, false);
  delay(2000);
  Serial.println("Disengaging motors");
  requested_state = AXIS_STATE_IDLE;
  odrive.run_state(0, requested_state, false);
  odrive.run_state(1, requested_state, false);
  delay(2000);
}
*/

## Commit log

2020-12-18 Initial commit, documenting setup of BLDC controller
2020-12-19 Backed up full ODrive config with wheel motor calibrations
    [odriveconfig.json]
2020-12-31 added drawings
    [base_board_cad.scad, common.scad, middle_board_cad.scad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]
2021-01-17 Refactoring raw sensor reading
2021-01-23 Experiments with Madgwick filter
2021-02-06 Getting logging working, ahrs not correct
    [AHRS.cpp, main.cpp]
2021-02-13 Switched to native i2c api, moved ahrs performance test to test project
2021-02-14 serial cxn to odrive and motor mvmt established
2021-02-20 Testing sending commands to odrive, cs mech not working
    [main.cpp]
2021-02-21 Odrive ascii serial motor control working
2021-02-28 FXAS2100 gyro support added
2021-04-21 Added calibration tool for gyro and magnetometer
2021-04-24 Calibration tool with serial output, ahrs system still needs work
2021-05-02 Motor controller api written
2021-05-03 Starting PID controller
2021-05-08 WIP on PID controller and Observer pattern for AHRS
2021-05-15 Calibration of in-situ ahrs sensors
2021-05-18 Tweaks to PID, further testing
2021-05-21 Finished 3d print design for battery mounts
    [power4all.dxf, power4all.scad, power4allmount.scad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]
2021-05-22 Improvements to battery mount 3d model
    [power4allmount.scad, power4allmount.stl]
2021-05-29 Restored linear PID
2023-03-31 Updated calibration from new instructions following firmware update. Motor control working again
    [odriveconfig.json]
2023-04-13 WIP: Replaced Pi4 with Teensy MCU and prototype firmware
    [base_board_cad.scad, common.scad, middle_board_cad.scad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]
2023-04-22 Ready for MCU mvp functionality balance test
    [prototype_breadboard_mount.stl, prototype_powerbank_mount.scad]
2023-04-23 Proper ODrive setup code added
